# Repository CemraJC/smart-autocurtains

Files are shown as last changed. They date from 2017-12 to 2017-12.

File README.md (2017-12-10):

# Smart Auto-curtain System

A foundational system for controlling a stepper motor based on remote input,
ambient light readings and locally measured temperature.

Every curtain system is different, so some independent design is required.

**Please read this whole document before building! Seriously!** (I mean, c'mon,
it's not that long - it'll save you a bunch of time in the setup)

## What it does

The basic system will open or close curtains based on remote control input. In
the event of remote control failure, the system has two integrated buttons to
operate the curtains.

**However,** the system can do much more than simple remote operation. If
"Auto-brightness control" is enabled, the system will close the blinds if
outside light levels exceed a pre-determined threshold. This is to assist with
sleeping in bright-early environments.

Also, depending on the local temperature (and your currently active settings),
the system may open the blinds to allow sunlight or air circulation.

Note that the system does not use the local time to operate, because the
hardware required adds unnecessary complexity to the setup and user operation of
the system.

## System components:

1. Arduino Nano
    * Could be substituted for a different type of Arduino
    * Minimum specs:
    * Must have a regulated power supply
2. Stepper Motor and controller (more info - todo)
3. 5V power supply and cable (more info - check max rating for stepper)
4. 2 momentary push buttons
5. 1 photoresistor
6. 1 temperature sensor
7. 1 IR LED (for receiving remote signals)
8. 1 RGB LED (or 3 separate red, green, blue LEDs - diffused!)
9. Arbitrary IR remote (buttons will be programmed in)
10. Perforated circuit board (minimum 300x250)
11. Solid-core wire (cleaner than stranded)
12. Resistors (220, 1k, 10k)
13. Cardboard / MDF (more info when final casing completed)
14. Bump-press limit switch (for homing the system)

## Tools required:

1. Soldering Iron and Small Fan (to evacuate soldering smoke)
2. Wire strippers (optional, but highly recommended)
3. Screwdriver

## Building (TODO)

# Set-up procedure

The Smart Autocurtains require the following setup:

* Set the remote buttons
* Set the "away" position

These settings are saved in the Arduino's non-volatile memory, so the settings
are not wiped in a loss-of-power event. In other words, you should only have
to set up the system once.

Before attempting setup, make sure that the power is on. The system should
flash a green LED once when the power is turned on. Then, the curtains will
automatically seek the home position. If it is the first run, a red LED should
turn on next.

## Setting remote buttons

When you first run the system (or run it after a user-reset), you will need to
record the buttons on your remote. Every remote is different, however this
should still be a simple procedure. If you have difficulties, try changing the
remote you are using and making sure the remote is functional.

To check that your remote has battery, point a smartphone camera at the IR LED
on the front. Then, press a button. If the camera shows a flash, then the
remote is functional.

Some remotes are more reliable than others. Hold the remote a least 2 feet
(0.5 meters) away from the IR receiver and press each button quickly.

To record which buttons do what, follow these steps:

1. Observe that a red LED is lit up on the device (first run only)
1. Press the button on the remote that you want to correspond to "open"
1. Keep pressing this button (it needs four consecutive signals). If the LED flashes Red/Blue (Purple) then the remote sent a partial signal and you need to start again. Make sure that each press is quick.
1. Observe that the system flashes a blue LED exactly once
1. Choose and press the "close" button on the remote (4 times again)
1. Observe that the system flashes a blue LED exactly twice
1. Choose and press the "cancel" button (same deal as with the others)
1. Observe that the system flashes a blue LED exactly three times
1. Choose and press the "auto-dawn" button (to enable/disable closing the curtains when it gets bright in the morning)
1. Observe that the system flashes a blue LED exactly four times
1. Choose and press the "auto-temp" button (to enable/disable force-opening the curtains when the temperature exceeds 28 degrees C)
1. Observe that the system flashes a blue LED exactly five times and the curtains proceed to the home position

Note that it will take about 30 seconds for the settings to be saved into the
permanent memory, so don't power down the system at least until then.

**Important:** on first run, be prepared to quickly power down the system in
the event that the homing switch does not function correctly. If the stepper
is allowed to run past home, it may stall and/or cause damage to the device or
your curtains.

Now is a good time to mention that we take no responsibility for any damages
caused by the system (although, to be fair, it's pretty unlikely that anything
seriously bad could happen).

## Setting home and away positions

#### What are home and away positions?

The curtains have two key positions, "home" and "away". The home position is
set by where the homing switch is placed. Depending on how the system is set
up, home and away could be in very different places. Regardless, home is the
position the curtains should be in when _open_. Home is set automatically by
the system, assuming the limit switch is properly in place.

Once home is found (the system re-homes every time on startup), the "away"
position must be set by the user (if it has not been already). 

#### How to set the away position

To set the away position, wait for the "red blue" LED sequence (purple on an
RGB system) and then proceed to press and hold the open/close buttons (on the
remote, or the onboard buttons) to set the away position. If the directions
are wrong (i.e the open button closes the curtains) then you will need to
switch the rails to which the curtains are clipped.

_Note:_ Holding down a button may not work on some remotes. In this case, you
will need to repeatedly press the open/close remote buttons to step the
curtains into the desired position. Alternatively, press and hold the onboard
system buttons (this should always work).

Once you are happy with the curtain's position as the "away" position, press
and hold both onboard buttons for 2 seconds. The away position is now set, it
should not need to be set again (unless you reset the system).

## All done!

When the away position is set successfully, the device should flash a green
LED. Your Smart Autocurtains are now ready for use!

# How to use the Smart Autocurtains

Once the curtains are set up according to the above procedure, you can operate
the curtains in the following ways:

## Using the remote

With a single press of the open or close buttons, the curtains will travel the
full distance to the home/away position respectively. If you only want the
curtains, say half-open, then press the cancel button halfway through the
motion.

Once a motion is canceled, a subsequent motion will pick back up from where
the curtains currently are.

Note that, since this system is designed to be flexible, remote performance is
not always as good as if it was a native system.

## Using the on-board buttons

There are two buttons, one to open, and one to close. If both buttons are
pressed at once, the curtains will cancel their current motion (assuming there
is one being made).

**WARNING:** When you first press a button, the system needs time to wake up
from low power mode. Because of this, you may need to hold one of the buttons
for at most 1 second to get the system to respond. The system will re-enter
low power mode after 10 seconds of no user input.

If both buttons are pressed and held for 4 seconds, the entire system should
reset - including clearing all settings, remote buttons and positions. The
system will need to be setup from scratch if reset in this way.

## With the "smart" features

There are two smart features, "autodawn control" and "autotemp control". These
smart features operate the curtains without user input in response to readings
from light and temperature sensors.

To **enable/disable** these features individually, press the corresponding buttons
on the remote that were recorded during setup and observe that the system
should flash a red or green LED for "off" or "on" respectively.

## Autodawn

This feature is the reason this system exists. Where I (the developer) live,
it gets fairly bright at around 4 or 5am. I prefer to wake up at 7am, but the sun
won't let me. You get the idea.

The system uses a light sensor to determine if it is currently night. It does
this by waiting for the light levels to drop below a "night-time" threshold
for a minimum of 30 minutes. If it is night (or the system _thinks_ it is),
then the curtains will open, to allow air circulation.

Then, when light levels exceed the "night-time" threshold level for at least
30 minutes, the system will close the blinds to prevent early-brightness from
waking you up.

## Autotemp

Having the curtains closed for brightness is only good as long as the
temperature is bearable. Based on external research, 28 degrees C is a general
threshold at which humans find it difficult to sleep. For this reason, if
autotemp is enabled, the curtains will be forced to open to allow air
circulation - regardless of autodawn. Of course, user input will override the
auto-temp setting (for up to 1 hour) unless autotemp is disabled, and then re-
enabled.

Whether or not this feature makes sense for you depends on your unique
circumstance. It also assumes that your windows are actually open - otherwise,
all it does is let in sunlight and make things worse!

# Common Issues

## I have to hold the on-board button before it works

This is normal. When you first press a button, the system needs time to wake
up from low power mode. Because of this, you may need to hold one of the
buttons for at most 1 second to get the system to respond. The system will re-
enter low power mode after 10 seconds of no user input.

## My remote doesn't work when I try to set it up

Try another remote. The system should recognize most remotes, but there are a
few whacky ones out there that don't work for some reason. If you can't get a
_normal_ Infra-Red TV remote to work, and you've tried other remotes, then you
may need to reset the system.

## My remote doesn't work anymore - it used to!

To check that your remote has battery, point a smartphone camera at the IR LED
on the front. Then, press a button that you have recorded on the system. If
the camera shows a flash, then the remote is functional.

If your remote is working, but the system is not responding, then try holding
the remote really close to the IR receiver on the device, shielding if from
the environment with your hand. If this fixes the problem, you will need to
identify possible sources of infra-red interference and remove them from the
environment.

If the system still doesn't work, follow the troubleshooting procedure below
to cycle the power, and if necessary, reset the entire system.

## I have some other problem

Follow the troubleshooting procedure below. If this still does not resolve
your issue, then I'm out of ideas. If you find a problem that is not resolved
by following the procedure below, don't hesitate to open a GitHub Issue and I
will try to work with you to resolve the problem.

# Troubleshooting

## Deep cycle the power

If the system is malfunctioning, follow these steps to try and resolve the issue:

1. Turn the system off with the power switch, then turn off the switch at the wall.
2. Wait for 5 seconds to ensure all power has drained from the system
3. Turn the wall switch back on (nothing should be happening yet)
4. Turn the device's power switch back on

Now, you should see the system flash a green LED twice and the system should
go to home.

## Well, that didn't fix it.

Press and hold the onboard buttons for 4 seconds. The system should flash a
red LED twice, then reset itself - clearing all settings. Then, go through the
setup procedure again and see if the system is now functioning correctly.

You should not have to do this often/at all. If you find yourself regularly
doing this, then check that the stepper is rotating _continuously_ (i.e. no
jumpiness or skips) when opening/closing the curtains. If it does not rotate
continuously, then you will need to reduce the torque on the stepper by either
adjusting the curtains, so they move with less friction, or by upgrading the
stepper motor to one with higher torque. A stepper upgrade is difficult work,
and is left as an exercise only to advanced users. 

## Something is probably broken.

If there are no green flashes on startup, confirm that the LEDs are functional.
Still no flashes, then either there is something wrong with the code, or the
Arduino is malfunctioning - possibly due to loose connections, or a short
circuit. If you have made modifications to the code, you will need to debug it
yourself.

If you do see two green flashes, the system should move the curtains
to the home position. If the curtains do not move, and are not already at the
home position, check the wiring to the stepper motor and confirm that power is
being correctly applied.

If the wiring is correct, and still no motion, use your fingers to test the
temperature of the motor and all the IC's (integrated circuit chips). They
should all be at room temperature, or only slightly warm. If any of the chips
are too hot to touch, immediately power down the system and triple check the
wiring, paying careful attention to potential short circuits due to faulty
resistors/capacitors.

If the curtains move, but do not stop when they reach home (or they home too
early/at random positions) power down the system and confirm that the limit
switch is functioning correctly and is properly hooked up to the Arduino.

If the curtains do not reliably return to the home and away positions, go to
the previous section to check that the stepper is functioning correctly.

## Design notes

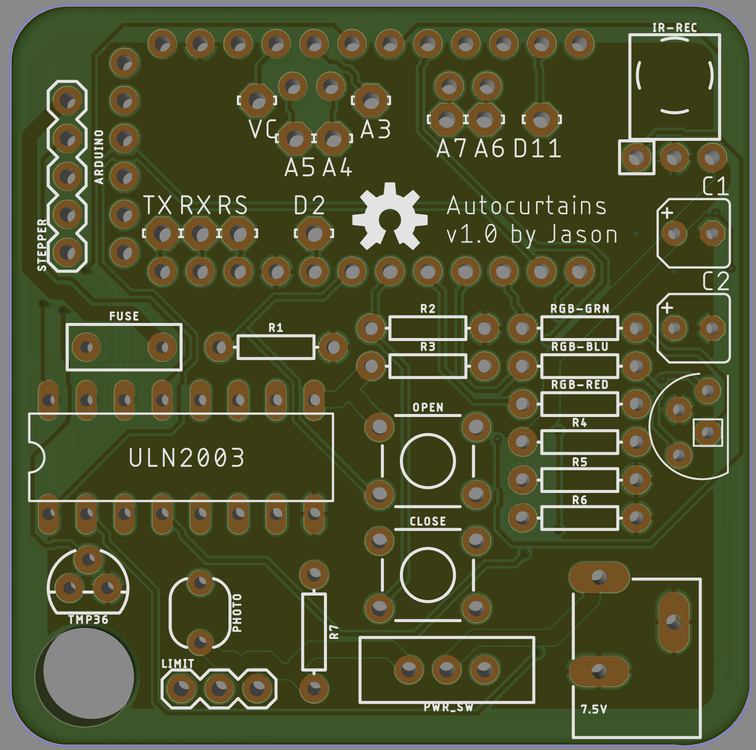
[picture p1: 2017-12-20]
pcb_images/front.png

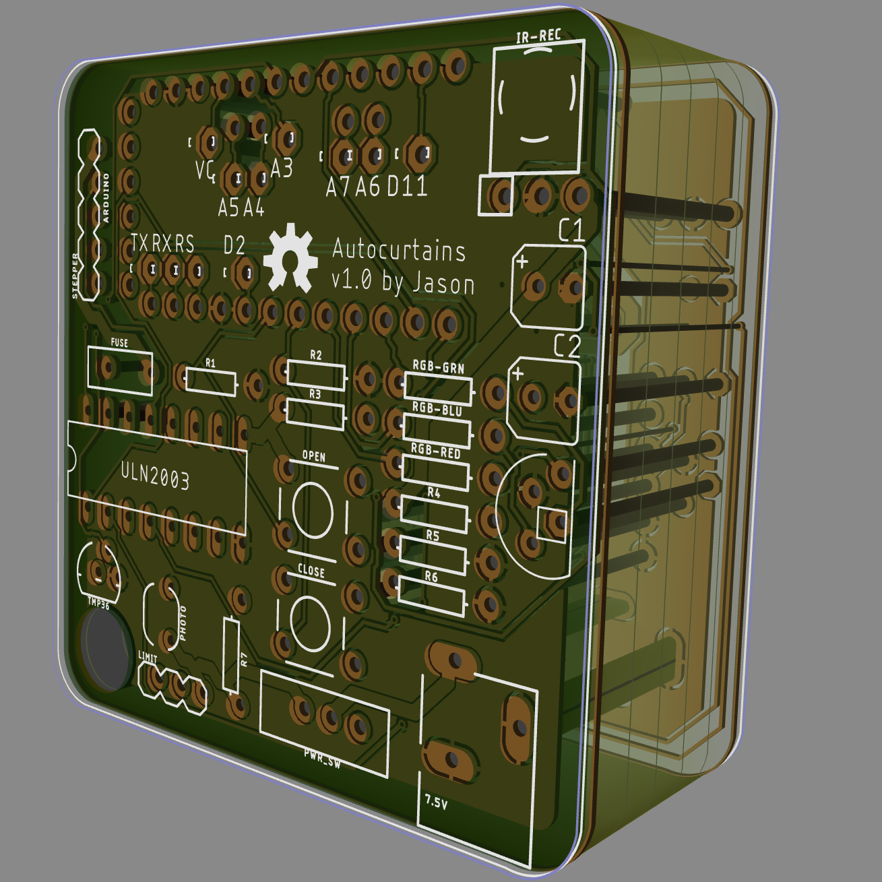
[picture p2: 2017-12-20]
pcb_images/profile_expanded.png

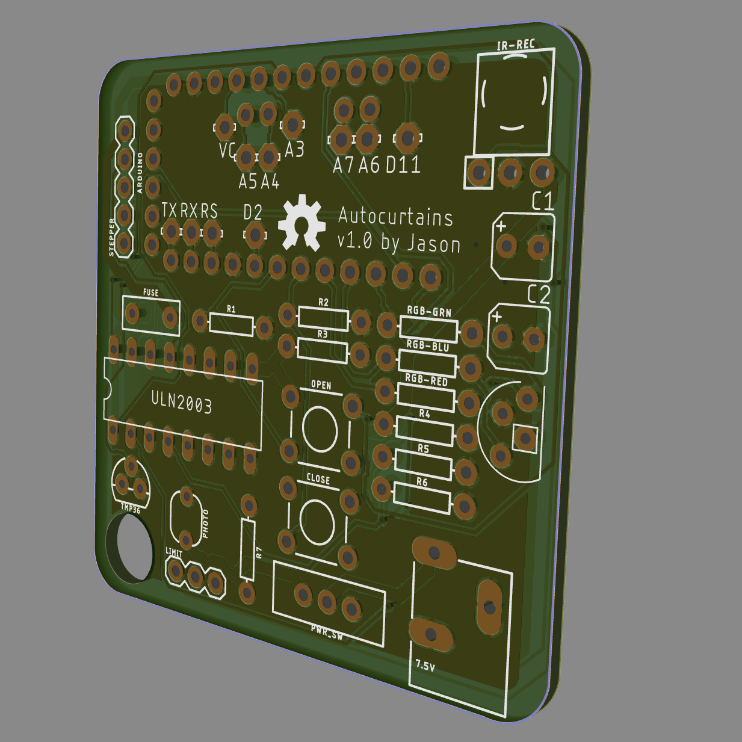
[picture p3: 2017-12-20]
pcb_images/profile.png

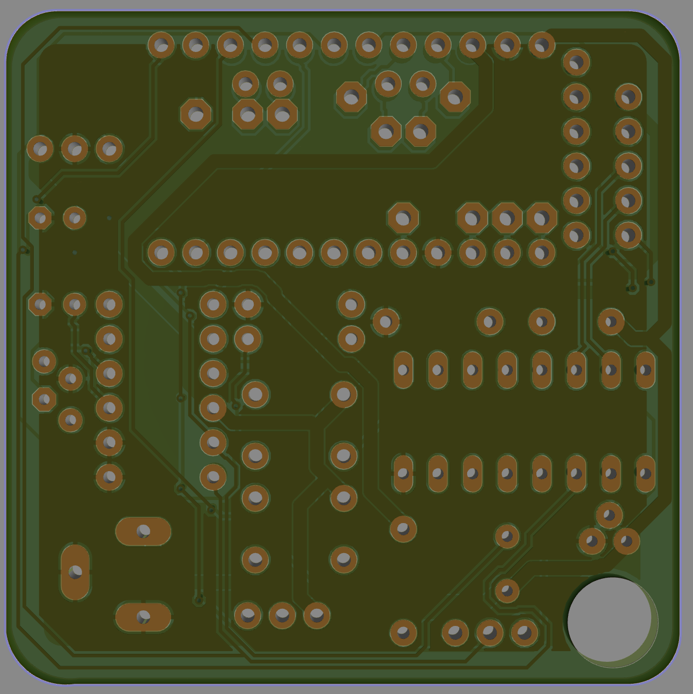
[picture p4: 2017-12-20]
pcb_images/back.png

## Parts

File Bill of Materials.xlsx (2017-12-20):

*All currency in AUD
Single Unit |  |  |  | Multi-units |  | Source |  |  |  | URL | Totals
Item Name | Item Price (1x) | Qty. Needed | Total Price | Qty. Needed | Total Price | Stock Qty. | Stock Price | Stock Units Needed | Item Source Price |  | Device Value | Total Price
Arduino Pro Mini | $2.18 | 1 | $2.18 | 2 | $4.36 | 1 | $2.18 | 2 | $4.36 | bit.ly/2ApPGsc-APM | $16.69 | $56.74
Stepper + Driver | $2.24 | 1 | $2.24 | 2 | $4.48 | 1 | $2.24 | 2 | $4.48 | bit.ly/2zduoQx-SMWD | Shipping: | $0.00
TMP36 Sensor | $1.30 | 1 | $1.30 | 2 | $2.60 | 1 | $1.30 | 2 | $2.60 | bit.ly/2o65BtP-TMP36 | Units | 2
2C Black Wire | $1.02 | 5 | $5.08 | 5 | $5.08 | 10 | $10.15 | 1 | $10.15 | bit.ly/2BsgtYs-2CW | Unit Price: | $28.37
Capacitors | $0.24 | 2 | $0.47 | 4 | $0.94 | 10 | $2.35 | 1 | $2.35 | bit.ly/2C9qIh5-CAPS
DC Barrel Jack | $0.05 | 1 | $0.05 | 2 | $0.11 | 45 | $2.39 | 1 | $2.39 | bit.ly/2CokPgO-DCBJ
7.5V DC Wall Plug | $2.99 | 1 | $2.99 | 2 | $5.98 | 1 | $2.99 | 2 | $5.98 | bit.ly/2jW6pgr-PWR7-5
Fuse Resistor | $0.18 | 1 | $0.18 | 2 | $0.37 | 10 | $1.84 | 1 | $1.84 | bit.ly/2kv6dEx-FR
Heat Shrink | $0.20 | 0.2 | $0.04 | 0.4 | $0.08 | 5 | $1.00 | 1 | $1.00 | bit.ly/2khBdbA-HS
IR Receiver | $0.11 | 1 | $0.11 | 2 | $0.22 | 10 | $1.09 | 1 | $1.09 | bit.ly/2B9Nnhn-IR
Limit Switch | $0.10 | 1 | $0.10 | 2 | $0.20 | 10 | $1.00 | 1 | $1.00 | bit.ly/2yTgxLv-LS
Momentary Button | $0.01 | 2 | $0.02 | 4 | $0.05 | 100 | $1.19 | 1 | $1.19 | bit.ly/2kgaSed-MTPB
Photoresistor | $0.05 | 1 | $0.05 | 2 | $0.10 | 20 | $1.00 | 1 | $1.00 | bit.ly/2oGm48y-PR
Resistors | $0.01 | 10 | $0.06 | 20 | $0.11 | 300 | $1.70 | 1 | $1.70 | bit.ly/2oGjfV4-AR
SPDT Switch | $0.05 | 1 | $0.05 | 2 | $0.10 | 20 | $1.00 | 1 | $1.00 | (need checking)
Custom PCB | $1.66 | 1 | $1.66 | 2 | $3.32 | 8 | $13.28 | 1 | $13.28 | dirtypcbs.com
RGB LED | $0.11 | 1 | $0.11 | 2 | $0.22 | 12 | $1.33 | 1 | $1.33 | bit.ly/2AYCqv2-RGB

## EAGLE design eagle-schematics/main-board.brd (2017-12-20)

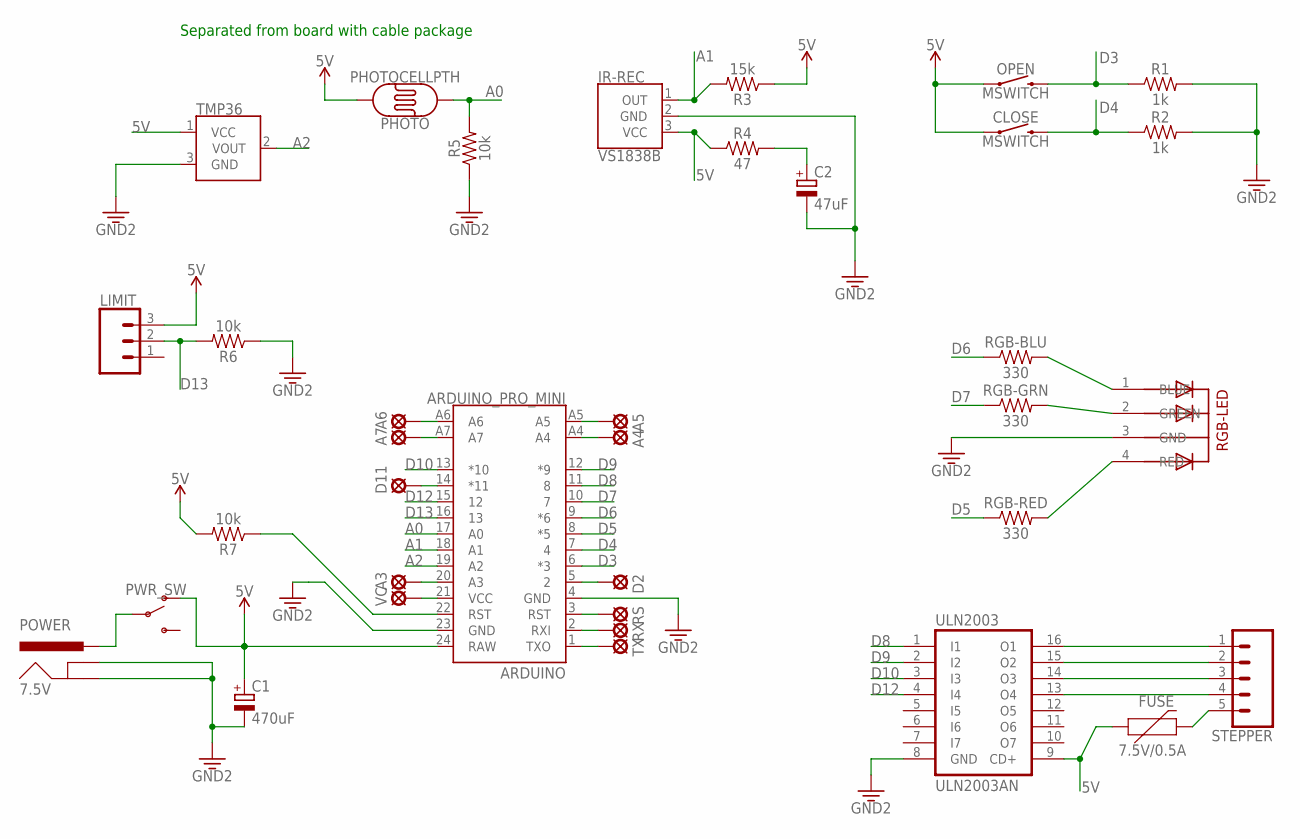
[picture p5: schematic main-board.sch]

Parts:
7.5V: POWER; POWER_JACK_SLOT
A3, A4, A5, A6, A7: LSP11
ARDUINO: ARDUINO_PRO_MINI
C1: 470uF; B45181A
C2: 47uF; B45181A
CLOSE: MSWITCH; TACTILE_SWITCH_PTH_6.0MM
D2, D11: LSP11
FUSE: 7.5V/0.5A; PTH
IR-REC: VS1838B; BRM-2508_VERT
LIMIT: CONN_03; 1X03
OPEN: MSWITCH; TACTILE_SWITCH_PTH_6.0MM
PHOTO: PHOTOCELLPTH; PHOTOCELL
PWR_SW: SWITCH-SPDT-PTH-11.6X4.0MM; SWITCH_SPDT_PTH_11.6X4.0MM
R1, R2: 1k; AXIAL-0.3
R3: 15k; AXIAL-0.3
R4: 47; AXIAL-0.3
R5, R6, R7: 10k; AXIAL-0.3
RGB-BLU: 330; AXIAL-0.3
RGB-GRN: 330; AXIAL-0.3
RGB-LED: DIFFUSE; LED5MMRGB
RGB-RED: 330; AXIAL-0.3
RS: LSP11
RX: LSP11
STEPPER: CONN_05; 1X05
TMP36: TMP36GT9; TO-92
TX: LSP11
ULN2003: ULN2003AN; DIL16
VC: LSP11

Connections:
5V: ARDUINO.24 (RAW), C1.+, CLOSE.1, FUSE.P$1 (1), IR-REC.3 (VCC), LIMIT.3, OPEN.1, PHOTO.2, PWR_SW.1 (O), R3.P$1 (1), R4.P$1 (1), R7.P$2 (2), TMP36.1 (VCC), ULN2003.9 (CD+)
A0: ARDUINO.17 (A0), PHOTO.1, R5.P$2 (2)
A1: ARDUINO.18 (A1), IR-REC.1 (OUT), R3.P$2 (2)
A2: ARDUINO.19 (A2), TMP36.2 (VOUT)
AFTER: ARDUINO.22 (RST), R7.P$1 (1)
D3: ARDUINO.6 (*3), OPEN.3 (2), R1.P$1 (1)
D4: ARDUINO.7 (4), CLOSE.3 (2), R2.P$1 (1)
D5: ARDUINO.8 (*5), RGB-RED.P$1 (1)
D6: ARDUINO.9 (*6), RGB-BLU.P$1 (1)
D7: ARDUINO.10 (7), RGB-GRN.P$1 (1)
D8: ARDUINO.11 (8), ULN2003.1 (I1)
D9: ARDUINO.12 (*9), ULN2003.2 (I2)
D10: ARDUINO.13 (*10), ULN2003.3 (I3)
D12: ARDUINO.15 (12), ULN2003.4 (I4)
D13: ARDUINO.16 (13), LIMIT.2, R6.P$2 (2)
FUSE: FUSE.P$2 (2), STEPPER.5
GND: 7.5V.GND@1 (GNDBREAK), 7.5V.GND@2 (GND), ARDUINO.4 (GND), ARDUINO.23 (GND), C1.-, C2.-, IR-REC.2 (GND), R1.P$2 (2), R2.P$2 (2), R5.P$1 (1), R6.P$1 (1), RGB-LED.3 (GND), TMP36.3 (GND), ULN2003.8 (GND)
unnamed: 7.5V.PWR, PWR_SW.2
unnamed: C2.+, R4.P$2 (2)
unnamed: RGB-BLU.P$2 (2), RGB-LED.1 (BLUE)
unnamed: RGB-GRN.P$2 (2), RGB-LED.2 (GREEN)
unnamed: STEPPER.1, ULN2003.16 (O1)
unnamed: STEPPER.2, ULN2003.15 (O2)
unnamed: STEPPER.3, ULN2003.14 (O3)
unnamed: STEPPER.4, ULN2003.13 (O4)
unnamed: RGB-LED.4 (RED), RGB-RED.P$2 (2)
unnamed: A6.MP, ARDUINO.A6
unnamed: A7.MP, ARDUINO.A7
unnamed: A5.MP, ARDUINO.A5
unnamed: A4.MP, ARDUINO.A4
unnamed: A3.MP, ARDUINO.20 (A3)
unnamed: ARDUINO.21 (VCC), VC.MP
unnamed: ARDUINO.5 (2), D2.MP
unnamed: ARDUINO.3 (RST), RS.MP
unnamed: ARDUINO.2 (RXI), RX.MP
unnamed: ARDUINO.1 (TXO), TX.MP
unnamed: ARDUINO.14 (*11), D11.MP

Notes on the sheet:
Separated from board with cable package

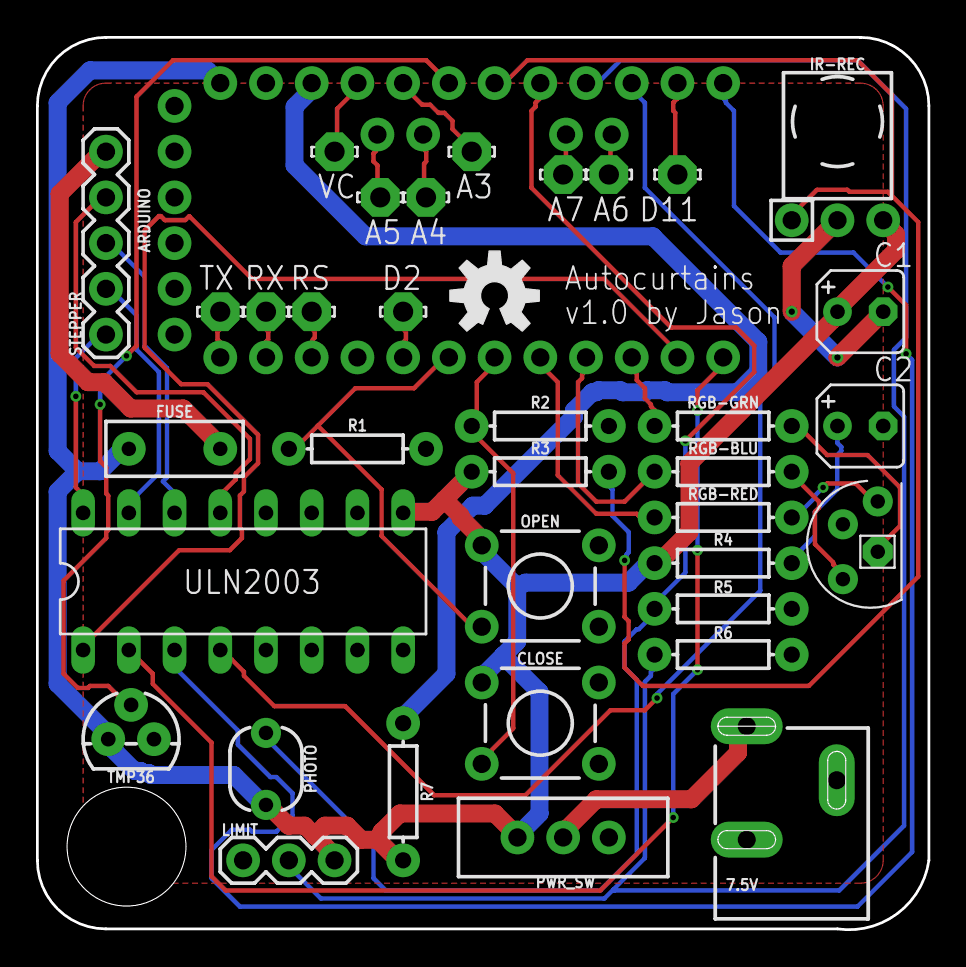
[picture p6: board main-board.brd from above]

Board: 2 copper layers, 49.5 x 49.6 mm, 37 parts (0 on the bottom side), 37 nets.

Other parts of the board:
U$1: OSHW-LOGO-M

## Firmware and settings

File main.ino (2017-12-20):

/* Need header comment! */

#include <RGBDisplay.h>
#include <InputControl.h>
#include <CurtainControl.h>

// For Development
#define DEBUGGING true

#if DEBUGGING
#	define DBG_PRINT(...)    Serial.print(__VA_ARGS__)
#	define DBG_PRINTLN(...)  Serial.println(__VA_ARGS__)
#else
#	define DBG_PRINT(...)
#	define DBG_PRINTLN(...)
#endif

// Controls for sleep mode
#define ACTIVE_LOOP 0 // delay in ms between loops in an active state
#define SLEEP_LOOP 250 // delay in ms between loops in a sleep state
#define SLEEP_TIME 10000 // time in ms to wait after input before going into low power (sleep) mode

#define RECORD_LOOPS 3 // Number of times need to check a button before recording

#define NO_HOLD_DEBOUNCE 500 // Time to wait after holding a button to allow pressing it again
#define SHORT_HOLD 2000 // ms to hold a button for to count as a "short hold"
#define LONG_HOLD 4000 // ms to hold a button for to count as a "long hold"
#define USER_CANCEL_DELAY 60*60*1000 // ms to wait before activating auto-features again

#define AUTOTEMP_THRESHOLD 30
#define AUTODAWN_OPEN_DELAY 3*60*60*1000 // 3 Hours before re-open`

RGBDisplay rgb_out(5,6,7); // r, g, b pins
UserInputControl input(3, 4, 13, 11); // Open, Close, Home and IR pins
SensorInputControl sensors(A0, A1); // Light pin, Temp Pin
CurtainControl curtain(8,9,10,12);  // Stepper pins 1,2,3 and 4

unsigned int loop_pause = 1; // For controlling the speed of the loop
bool autodawn_reopen_trigger = false; // If true, will reopen curtains after time is up (unless cancelled)
long remote_signal = 0;
bool setting_changed = false; // Track changes (no hold-down on settings)

void setup() {

	if (DEBUGGING) { Serial.begin(9600); };

	DBG_PRINTLN("Starting initialization...");
	input.init();
	sensors.init();
	curtain.init(); // Settings will be read if they are present.
	rgb_out.init();
	DBG_PRINTLN("Finished initialization.");

	// Manual blocking flash is OK
	rgb_out.solid(0, 1, 0);
	delay(200);
	rgb_out.off();

	DBG_PRINTLN("Homing Curtains.");
	home_curtains();
	DBG_PRINTLN("Homing Complete.");

	if (curtain.settings.away == 0 && curtain.settings.remote_open == 0) { // Then it's the first run
		DBG_PRINTLN("First run. Learning signals and away position.");
		record_remote();
		record_away();
		curtain.trigger_write();
	} else if (curtain.settings.away == 0 && curtain.settings.remote_open != 0) { // Need to redo away position!!
		record_away();
		curtain.trigger_write();
	}
}

void loop() {

	// Control the low power (sleep) state of the system
	if (loop_pause != ACTIVE_LOOP && (input.time_since_input() < SLEEP_TIME || curtain.is_moving())) {
		DBG_PRINTLN("Waking From Sleep Mode");
		loop_pause = ACTIVE_LOOP;
	} else if (loop_pause != SLEEP_LOOP && input.time_since_input() >= SLEEP_TIME && !curtain.is_moving()) {
		DBG_PRINTLN("Entering Sleep Mode");
		loop_pause = SLEEP_LOOP;
	}

	// Get signal from the remote
	// Signals only last for a single loop
	if (input.new_signal()) {
		remote_signal = input.remote_signal();
	} else {
		remote_signal = 0;
	}

	// Handle open/close/cancel requests
	if (input.open_pressed() || remote_open()) {
		curtain.open();
		rgb_out.pip(1, 1, 1, 1, 500);
	} else if (input.close_pressed() || remote_close()) {
		curtain.close();
		rgb_out.pip(1, 1, 1, 1, 500);
	} else if (input.both_pressed() || remote_cancel()) {
		curtain.cancel();
		rgb_out.pip(1, 1, 1, 1, 500);
	}

	// Handle changes in settings
	if (!setting_changed && remote_autodawn()) {
		curtain.settings.autodawn = !curtain.settings.autodawn;
		DBG_PRINTLN(String("Settings Autodawn to ") + String(curtain.settings.autodawn));

		if (curtain.settings.autodawn) {
			Serial.println("Autodawn on pip");
			rgb_out.pip(0, 1, 0, 1, 500);
		} else {
			Serial.println("Autodawn off pip");
			rgb_out.pip(1, 0, 0, 1, 500);
		}

		rgb_out.update(); // Need to call straight away for some reason
		curtain.trigger_write();
		setting_changed = true;
	} else if (!setting_changed && remote_autotemp()) {
		curtain.settings.autotemp = !curtain.settings.autotemp;
		DBG_PRINTLN(String("Settings Autotemp to ") + String(curtain.settings.autotemp));

		if (curtain.settings.autotemp) {
			rgb_out.pip(0, 1, 0, 1, 500);
		} else {
			rgb_out.pip(1, 0, 0, 1, 500);
		}

		rgb_out.update();
		curtain.trigger_write();
		setting_changed = true;
	}

	// Allow settings changes again
	if (setting_changed 
		&& !remote_autodawn() && !remote_autotemp() 
		&& input.time_to_last_signal() > NO_HOLD_DEBOUNCE) {
		setting_changed = false;
	}

	// Reset timer (reset entire system after long hold)
	if (input.both_pressed() && input.time_to_last_press() >= LONG_HOLD) {
		reset_system();
	}

	// Autodawn feature
	if (curtain.settings.autodawn && input.time_since_input() >= USER_CANCEL_DELAY) {
		// If it was dark and getting light...
		if (!autodawn_reopen_trigger && sensors.is_light() && millis() - sensors.last_light_transition() < AUTODAWN_OPEN_DELAY) {
			// Close the curtains
			curtain.close();
			autodawn_reopen_trigger = true;
			DBG_PRINTLN("Autodawn: Close curtains, getting bright");
		} 

		// If we had closed the curtains and it's been enough time...
		if (autodawn_reopen_trigger && millis() - sensors.last_light_transition() >= AUTODAWN_OPEN_DELAY) {
			// Reopen the curtains
			DBG_PRINTLN("Autodawn: Reopen curtains, time's up.");
			curtain.open();
			autodawn_reopen_trigger = false;
		}
	}

	// Autotemp feature - open if temps get too high.
	if (curtain.settings.autotemp && input.time_since_input() >= USER_CANCEL_DELAY) {
		if (sensors.get_temperature() >= AUTOTEMP_THRESHOLD) {
			DBG_PRINTLN("Autotemp: Open curtains, too hot.");
			curtain.open();
		}
	}

	// Cancel any automatic functions
	if (input.time_since_input() <= USER_CANCEL_DELAY) {
			autodawn_reopen_trigger = false;
	}

	curtain.poll();
	rgb_out.update();

	// Variable delay for low power (sleep) mode.
	delay(loop_pause); 
}

// Records the remote buttons into the settings (and trigger a save)
void record_remote() {
	unsigned short seq_num = 1;
	long signal;
	long last_signal = 0;
	unsigned short signal_count = 0;

	rgb_out.solid(1, 0, 0);	

	while (seq_num <= 5) {
		if (input.new_signal()) {

			signal = input.remote_signal();

		    DBG_PRINT("Received: ");
		    DBG_PRINTLN(signal, HEX);

			// Make sure we haven't recorded the signal before:
			// (C++ is hard. This code is terrible, I know.)
			if (signal == curtain.settings.remote_open
			 || signal == curtain.settings.remote_close
			 || signal == curtain.settings.remote_cancel
			 || signal == curtain.settings.remote_autodawn
			 || signal == curtain.settings.remote_autotemp) {
				    DBG_PRINTLN("Tried to record an already recorded signal");
					signal_count = 0;

					// Yellow flash
			    	rgb_out.solid(1, 1, 0);
			    	delay(500);
			    	rgb_out.solid(1, 0, 0);
			    	continue;
			}

			if (signal == last_signal && signal_count < RECORD_LOOPS) {
			    DBG_PRINTLN("Success - inc. signal count.");
				++signal_count;

				// Single flash, ACK receive.
				rgb_out.solid(1, 1, 1);
		    	delay(25);
		    	rgb_out.solid(1, 0, 0);
			} else if (signal == last_signal && signal_count >= RECORD_LOOPS) {
				switch (seq_num) {
					case 1:
						curtain.settings.remote_open = signal;
						break;
					case 2:
						curtain.settings.remote_close = signal;
						break;
					case 3:
						curtain.settings.remote_cancel = signal;
						break;
					case 4:
						curtain.settings.remote_autodawn = signal;
						break;
					case 5:
						curtain.settings.remote_autotemp = signal;
						break;
				}

				signal_count = 0;
			    last_signal = 0;

				DBG_PRINT(String("Recorded signal for seq ") + String(seq_num) + String(" "));
				DBG_PRINTLN(signal, HEX);

				// Blocking flash (number of sequence)
				rgb_out.off();
				delay(250);
				rgb_out.pip(0, 0, 1, seq_num, 250);
				while (rgb_out.is_flashing()) {
					rgb_out.update();
				}
				rgb_out.solid(1, 0, 0);

				++seq_num;
				continue;
			} else if (signal != last_signal && signal_count > 0) { 
			    DBG_PRINTLN("Failure - reset signal count, start over.");
			    signal_count = 0;
			    last_signal = 0;

			    // Purple flash
				rgb_out.solid(1, 0, 1);
		    	delay(500);
				rgb_out.solid(1, 0, 0);
				continue;
			} else if (last_signal == 0) {
				++signal_count;
				last_signal = signal;

				// Single flash, ACK receive.
				rgb_out.solid(1, 1, 1);
		    	delay(25);
		    	rgb_out.solid(1, 0, 0);
			} else {

				// Single flash, ACK receive.
				rgb_out.solid(1, 1, 1);
		    	delay(25);
		    	rgb_out.solid(1, 0, 0);

				last_signal = signal;
			}
		}
	}

	rgb_out.off();

	DBG_PRINTLN("Finished recording remote. Signals:");
	DBG_PRINT("Open: ");
	DBG_PRINTLN(curtain.settings.remote_open, HEX);
	DBG_PRINT("Close: ");
	DBG_PRINTLN(curtain.settings.remote_close, HEX);
	DBG_PRINT("Cancel: ");
	DBG_PRINTLN(curtain.settings.remote_cancel, HEX);
	DBG_PRINT("Autodawn: ");
	DBG_PRINTLN(curtain.settings.remote_autodawn, HEX);
	DBG_PRINT("Autotemp: ");
	DBG_PRINTLN(curtain.settings.remote_autotemp, HEX);
	DBG_PRINTLN();
}

// Records the away position into the settings (and trigger a save)
void record_away() {
	rgb_out.solid(0, 0, 1);
	DBG_PRINTLN("Recording away position.");

	// Need to hold cancel on remote or buttons for SHORT_HOLD ms for this to exit
	while (true) {

		// Get signal from the remote
		// Signals only last for a single loop
		if (input.new_signal()) {
			remote_signal = input.remote_signal();
		} else {
			remote_signal = 0;
		}

		if (input.open_pressed() || remote_open()) {
			curtain.step(true);
		} else if (input.close_pressed() || remote_close()) {
			curtain.step(false);
		} else if (input.both_pressed() || remote_cancel()) {
			curtain.cancel();
		}

		if (input.both_pressed() && input.time_to_last_press() >= SHORT_HOLD) {
			break;
		} else if (remote_cancel() && input.time_to_last_signal() >= SHORT_HOLD) {
			break;
		}

		curtain.poll();
	}

	curtain.settings.away = curtain.get_location();
	DBG_PRINT("Away position set: ");
	DBG_PRINTLN(curtain.settings.away);

	rgb_out.off();
}

void home_curtains() {
	// We expect that a home switch will eventually
	// be pressed! If it is not, then bad things may happen.
	curtain.blind_rotate(true);
	rgb_out.pip(1, 0, 1);
	
	while (!input.home_pressed()) {
		curtain.poll();
		rgb_out.update();
	}

	rgb_out.off();
	curtain.cancel();
	curtain.set_home();
}

// Clears the EEPROM and restart the system
void reset_system() {
	rgb_out.solid(1, 0, 0);
	delay(1000);
	curtain.reset_settings();
	soft_reset();
}

void soft_reset() {
	asm volatile ("  jmp 0");
}


/*
Checking remote values
- Just some functions that return true if 
  the specified signal was received last and not acted on.
*/

bool remote_open() {
	return remote_signal == curtain.settings.remote_open;
}

bool remote_close() {
	return remote_signal == curtain.settings.remote_close;
}

bool remote_cancel() {
	return remote_signal == curtain.settings.remote_cancel;
}

bool remote_autodawn() {
	return remote_signal == curtain.settings.remote_autodawn;
}

bool remote_autotemp() {
	return remote_signal == curtain.settings.remote_autotemp;
}


/*
DEBUGGING FEATURES
*/

void serial_print_eeprom() {
	for (int i = SETTINGS_ADDR; i < SETTINGS_END_ADDR; ++i) {
		Serial.print(String(i) + ": ");
		Serial.println(EEPROM[i]);
	}
}

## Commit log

2017-12-02 Stepper experiment complete
2017-12-03 Started EAGLE project
    [main-board.sch]
2017-12-04 README and RGB LED stuff
    [main-board.sch]
2017-12-06 Added Sensors to InputControl
2017-12-06 Updated Schematic and BOM
    [Bill of Materials.xlsx]
2017-12-06 Started work on CurtainControl
    [Bill of Materials.xlsx]
2017-12-07 Completed phase 1 of work on stepper library
2017-12-07 Implemented Homing Routine
2017-12-10 Fixed remote reliability issue with main loop
    [main.ino]
2017-12-19 Added EAGLE files
    [main-board.brd, main-board.sch]
2017-12-19 Updated BOM
    [Bill of Materials.xlsx, main-board.sch]
2017-12-19 Added images of PCB
2017-12-19 Added Gerber files (CAM Job)
    [main-board.GBL, main-board.GBO, main-board.GBP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]
2017-12-20 Updated PCB design
    [Bill of Materials.xlsx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]

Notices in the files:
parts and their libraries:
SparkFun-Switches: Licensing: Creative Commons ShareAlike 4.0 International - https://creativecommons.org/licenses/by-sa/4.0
